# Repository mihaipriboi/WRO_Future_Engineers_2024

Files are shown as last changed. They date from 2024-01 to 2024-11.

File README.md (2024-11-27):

<center><h1> Nerdvana Cancer 2024 </center>

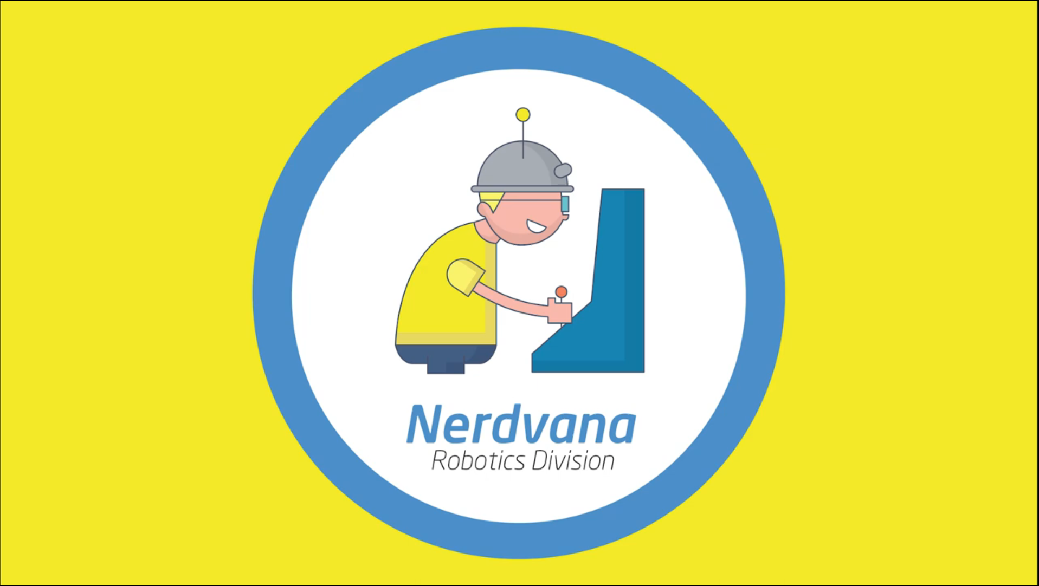
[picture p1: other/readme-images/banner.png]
Banner







This repository contains the documentation for the Nerdvana Cancer team's robot for the 2024 World Robot Olympiad Future Engineers competition. The robot, was designed and built by a team of three students.

## Table of Contents
* [The Team](#team)
* [The Challenge](#challenge)
* [The Robot](#robot-image)
* [Performance Video](#video)
* [Mobility Management](#mobility-management)
  * [Powertrain](#powertrain-mechanical)
    * [Drivetrain](#drivetrain-mechanical)
    * [Motor](#motor-mechanical)
    * [Motor Driver](#motor-driver-mechanical)
  * [Steering](#steering-mechanical)
    * [Servo Motor](#servo-motor)
  * [Chassis](#chassis-mechanical)
* [Power and Sense Management](#power-and-sense-management)
  * [Li-Po Battery](#li-po-battery)
  * [Arduino Nano ESP32](#arduino-nano-esp32)
  * [IMU](#imu-sensor)
  * [OpenMV Cam H7 R2](#openmv-cam-h7-r2)
  * [Voltage Regulator](#voltage-regulator)
  * [PCB Design](#pcb)
  * [Circuit Diagram](#circuit-diagram)
* [Code for each component](#code-for-each-component)
  * [Drive Motor](#drive-motor-code)
  * [Servo Motor](#servo-motor-code)
  * [Camera](#camera-code)
  * [IMU](#gyro-sensor-code)
* [Obstacle Management](#obstacle-management)
  * [Qualification Round](#quali-management)
  * [Final Round](#final-management)
  * [Additional code](#additional-code)
* [Robot Construction Guide](#robot-construction-guide)
  * [Step 0: Print the 3D parts](#3d-printing)
  * [Step 1: Assemble the steering system](#steering-system-assembly)
  * [Step 2: Assemble the powertrain](#powertrain-assembly)
  * [Step 3: Attach the electronics](#electronics-attachment)
  * [Step 4: Attach the wheels](#wheel-attachment)
  * [Step 5: Final touches](#final-touches)
  * [Step 6: Upload the code](#code-upload)
* [Cost Report](#cost-report)
  * [3D Printing Costs](#3d-printing-costs)
  * [Other Parts Tested](#other-parts-tested)
  * [Tools and Equipment](#tools-and-equipment)
  * [Summary of Costs](#summary-of-costs)
* [Randomizer](#randomizer)
* [Resources](#resources)
  * [3D Models](#3d-models-resources)
  * [Images](#images-resources)
* [License](#copyright)

---

## The Team 

### Nicola Victor Teodor
<p align="center">
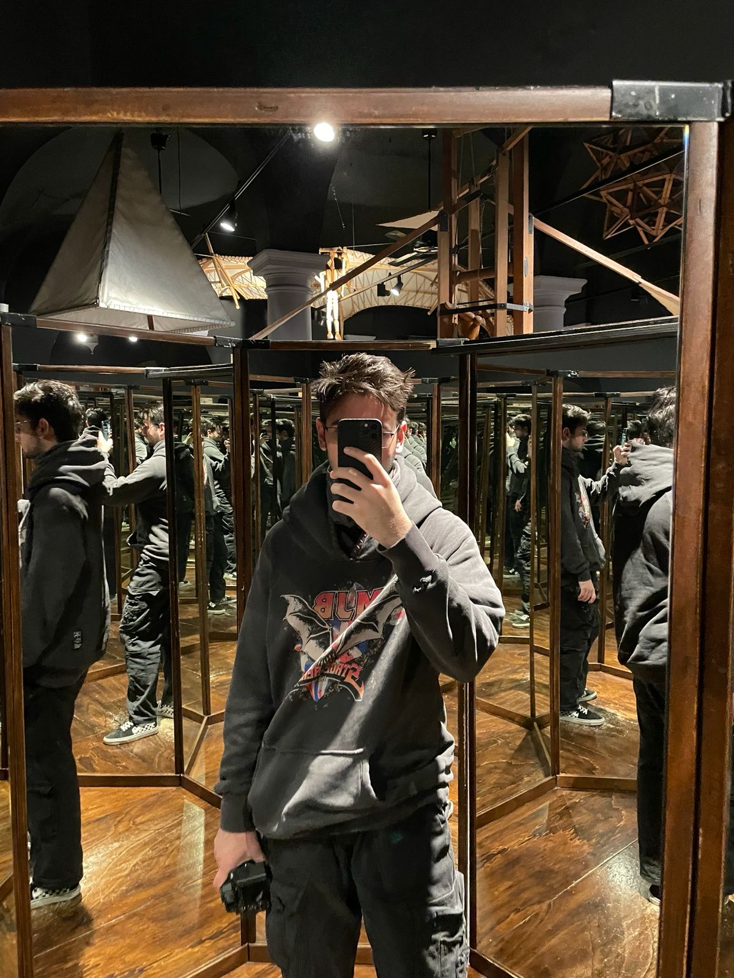
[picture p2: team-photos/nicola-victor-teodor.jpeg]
Nicola Victor Teodor
  
</p>

<b>Age:</b> 18

<b>High School:</b> National College of Informatics "Tudor Vianu", Bucharest

<b>Description:</b> Hi! I’m Victor from Romania and this is my second WRO season. Last year I participated in the RoboMission category and this year I wanted a new challenge. I own the fact that I’m a huge nerd: from coding and robotics, to photography, cinema, music, guitar, and even Formula 1.

---

### Bălan Teodor Ovidiu
<p align="center">
  Bălan Teodor Ovidiu
</p>

<b>Age:</b> 19

<b>University:</b> University of Bucharest

<b>Description:</b> Wassup y'all! My name is Teodor, and I love traveling and experiencing new things. Since I was a kid, I’ve always been drawn to solving puzzles, playing basketball, discovering new inventions, and thinking of creative ways to do things. Also, I know how to do a backflip. 🤠

---

### Priboi Luca Mihai
<p align="center">
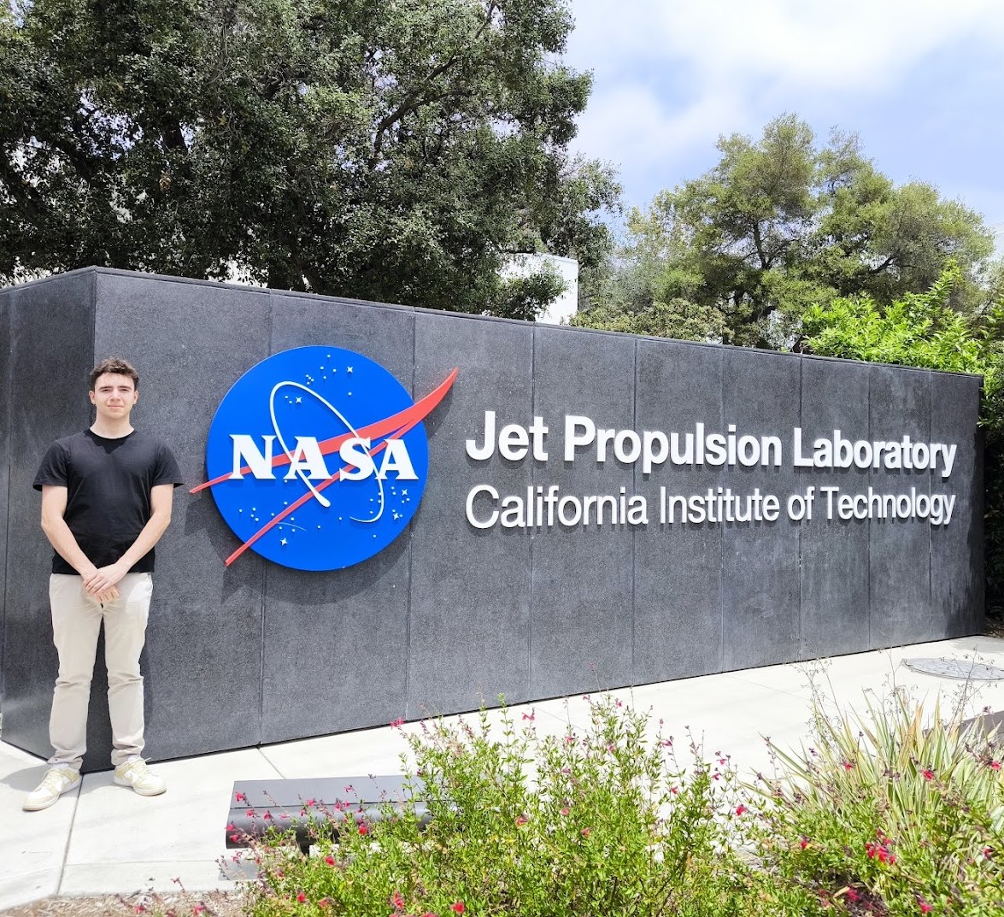
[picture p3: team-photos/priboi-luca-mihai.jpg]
Priboi Luca Mihai
  
</p>

<b>Age:</b> 19

<b>University:</b> Politehnica University of Bucharest

<b>Description:</b> Hello! I am Mihai! I've been participating at WRO since 2015 and I am very excited to be part of the Nerdvana Romania team. My academic passions are programming, physics and robotics, but I also enjoy playing the piano 🎹, whatching movies 🎬, traveling ✈️ and Formula 1 🏎️🏁.

---

### Tuțu Mihai Alexandru
<p align="center">
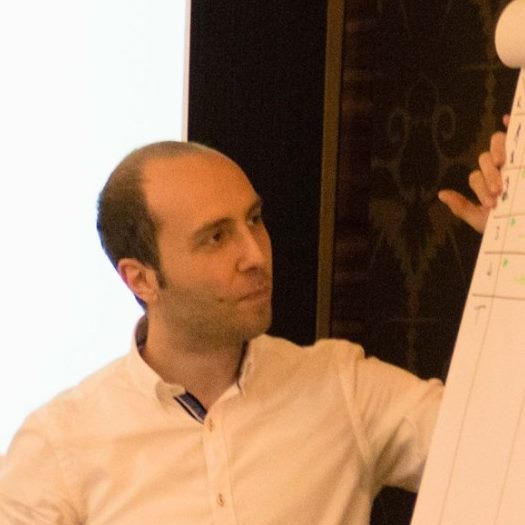
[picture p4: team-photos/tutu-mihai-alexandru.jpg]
Tuțu Mihai Alexandru
  
  <p align="center">Nerdvana Romania Founder</p>
</p>

<b>Role:</b> Coach

<b>Description:</b> Hard working young man, objective driven and ready for the long haul. I like challenges and I never back down. The harder, the better. I like being pushed over my limits just to prove myself I can do better.

Very social, I can easily blend in a team. Like to communicate a lot with others and to coordinate with other teammates. I was led and I led teams to certain objectives. I believe the only way to get where you want is to never stop trying and to never give up until you reach your destination.

---

### Priboi Maria Marcela
<p align="center">
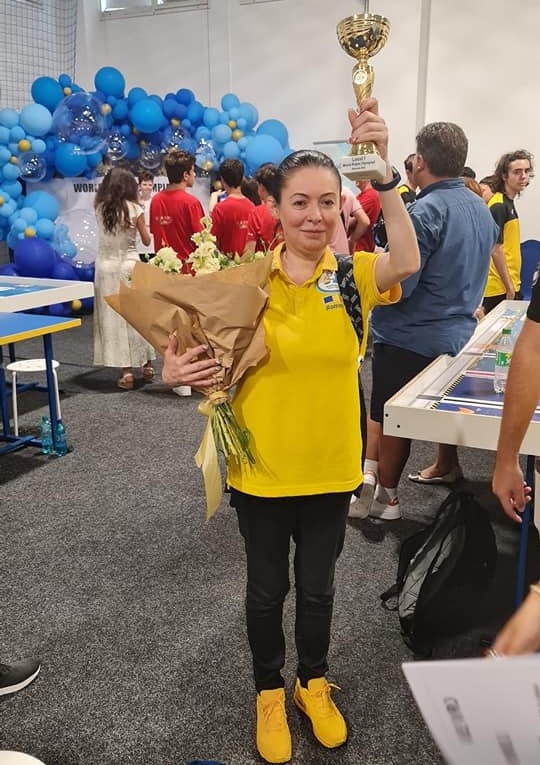
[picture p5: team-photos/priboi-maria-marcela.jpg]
Priboi Maria Marcela
  
  <p align="center">Nerdvana Romania Founder</p>
</p>

<b>Role:</b> Manager

<b>Description:</b> I am a very ambitious person, I like to work hard and to be involved in many projects. I am a very organized person and I like to have everything planned. I am a very sociable person and I like to communicate with people. I am a very responsible person and I like to take care of everything that is happening around me. I am a very creative person and I like to come up with new ideas. I am a very determined person and I like to achieve my goals.

---

### Team photo
<p align="center">
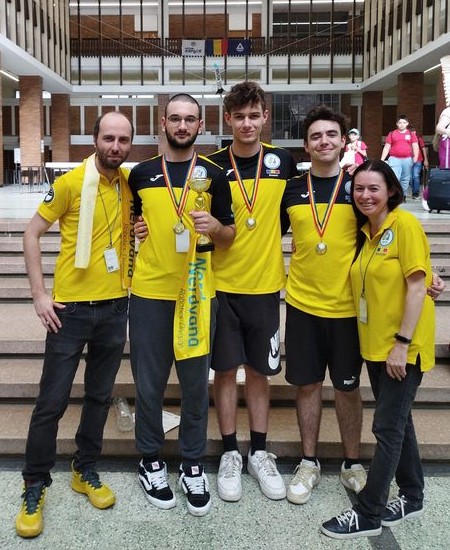
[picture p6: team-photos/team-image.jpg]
Team
  
</p>

## The Challenge 

The **[WRO 2024 Future Engineers - Self-Driving Cars](https://wro-association.org/)** challenge invites teams to design, build, and program a robotic vehicle capable of driving autonomously on a racetrack that changes dynamically for each round. The competition includes two main tasks: completing laps while navigating randomized obstacles and successfully performing a precise parallel parking maneuver. Teams must integrate advanced robotics concepts such as computer vision, sensor fusion, and kinematics, focusing on innovation and reliability.

This challenge emphasizes all aspects of the engineering process, including:
- **Mobility Management:** Developing efficient vehicle movement mechanisms.
- **Obstacle Handling:** Strategizing to detect and navigate traffic signs (red and green markers) within specified rules.
- **Documentation:** Showcasing engineering progress, design decisions, and open-source collaboration through a public GitHub repository.

Points are awarded based on performance in the challenge rounds, quality of the engineering documentation, and the ability to create an innovative and robust solution. The goal is to inspire STEM learning through real-world robotics applications, teamwork, and creative problem-solving.

Learn more about the challenge [here](https://wro-association.org/wp-content/uploads/WRO-2024-Future-Engineers-Self-Driving-Cars-General-Rules.pdf).

## Photos of our robot MOOYA (Mechanized Optimization for Outstanding Yield and Adaptation) 

|  |  | 
| :--: | :--: |
| *Front* | *Back* |
|  |  | 
| *Left* | *Right* |
|  |  | 
| *Top* | *Bottom* |

<br>

## Our video of the robot on [Youtube](https://www.youtube.com/watch?v=aLT0-nPUaAE) 

<br>

# Mobility Management 
<!-- ![Powertrain](./images/resources/powertrain.png "Powertrain") -->

The robot's mobility is managed by a combination of components, including the powertrain, steering system, and chassis. These elements work together to ensure the robot's smooth and efficient movement.

## Powertrain 

<!-- ![Powertrain - Bottom View](./images/resources/powertrain_bottom_text.png "Powertrain - Bottom View") -->

### Drivetrain 

To minimize friction and thereby reduce speed loss, driving axle was made from lego pieces. We conected the motor to the driving axle using a custom 3D-printed adapter. The driving axle has a rear wheel lego differential, which allows the robot to turn smoothly. As the axle was already lego, we used lego wheels.

<br>

**Potential Improvements**:
- Upgrade to a stronger or more precise differential for smoother turning.
- Test alternative materials for the Lego driving axle to reduce weight and increase durability.
- Replace the 3D-printed adapter with a metal one to improve robustness and reliability.

### Motor 

<table>
  <tr>
    <td width="50%" style="text-align: left;">
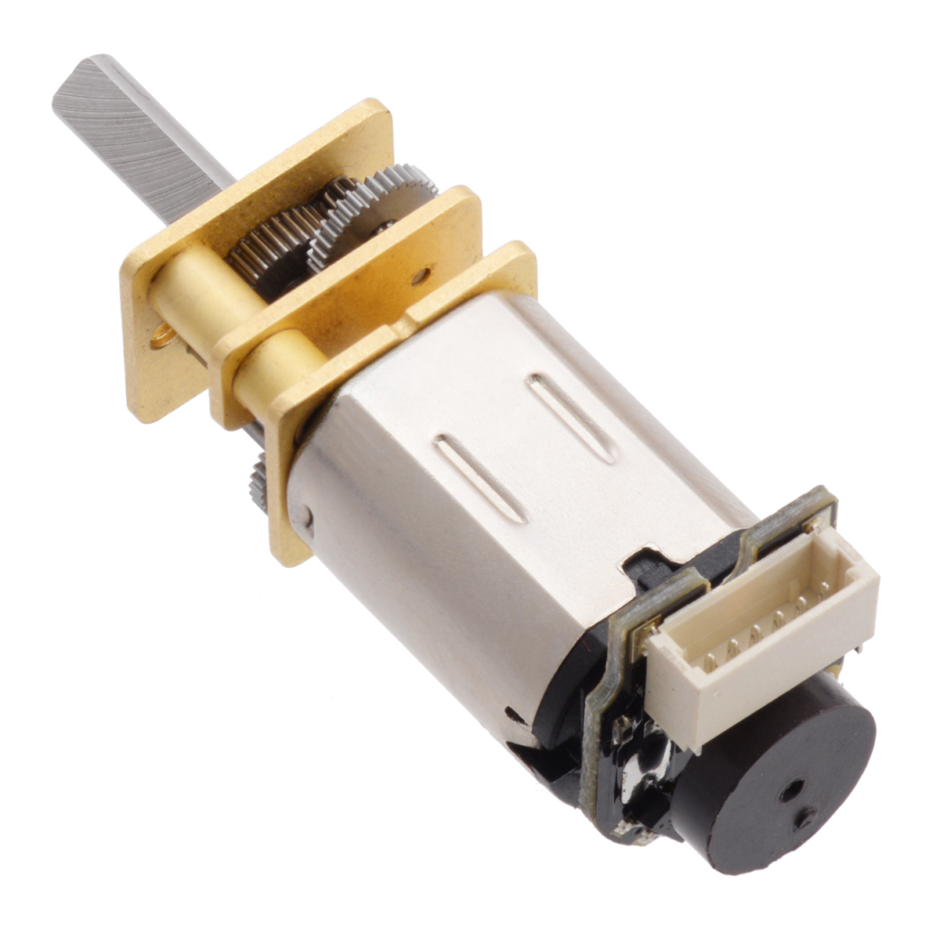
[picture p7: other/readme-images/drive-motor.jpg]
DC Gearmotor
      
    </td>
    <td width="50%" style="text-align: left; vertical-align: top;">
      <h3>Specifications:</h3>
      <li>Voltage: 12V</li>
      <li>Gear Ratio: 1:50</li>
      <li>Speed: 650 ± 31% rpm</li>
      <li>Torque: 0.67 ± kg·cm</li>
      <li>Weight: 9.5g</li>
      </li>
    </td>
  </tr>
</table>

Following an evaluation of different motors, we settled on a micro DC gear motor on which we attached a magnetic encoder. This motor was selected for its lightweight and compact design, which stands out among others with comparable output. Additionally, the magnetic encoder offers greater precision than its optical counterpart. We secured the motor to the chassis using a custom 3D-printed holder.

Where to buy the motor: https://www.pololu.com/product/3039

To connect the motor's axle to a Lego-compatible axle, we created a custom 3D-printed adapter.

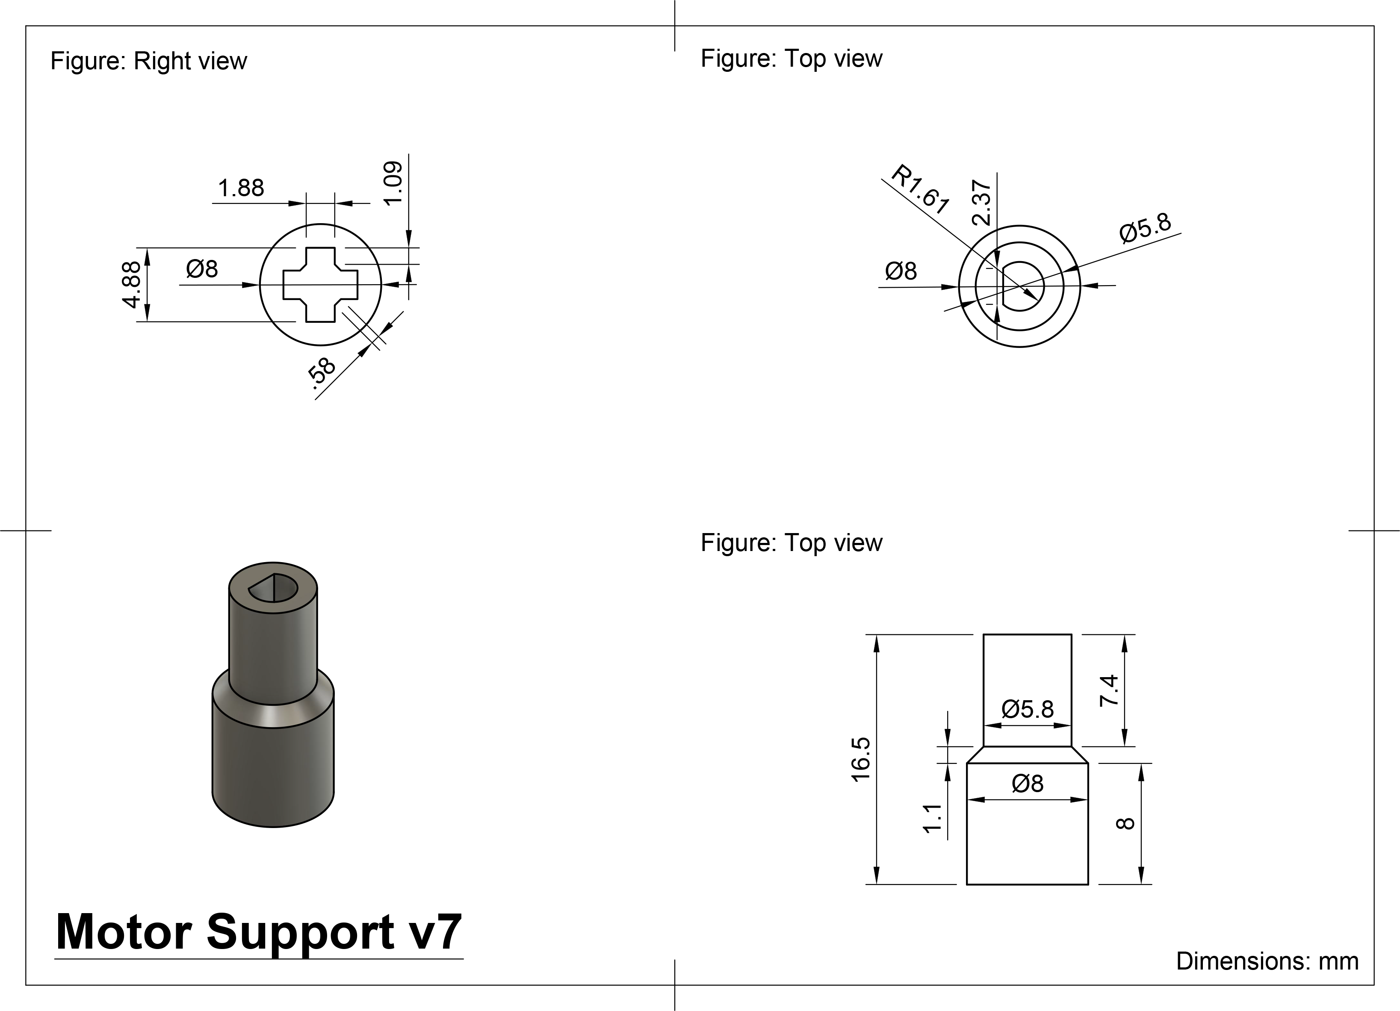
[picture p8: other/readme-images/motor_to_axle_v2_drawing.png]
Gearmotor to axle - 3D Model Gearmotor to axle 3D piece


To secure the motor to the chassis, we designed a custom 3D-printed holder. The holder is split into two halves, which are then screwed together to ensure the motor remains in place.

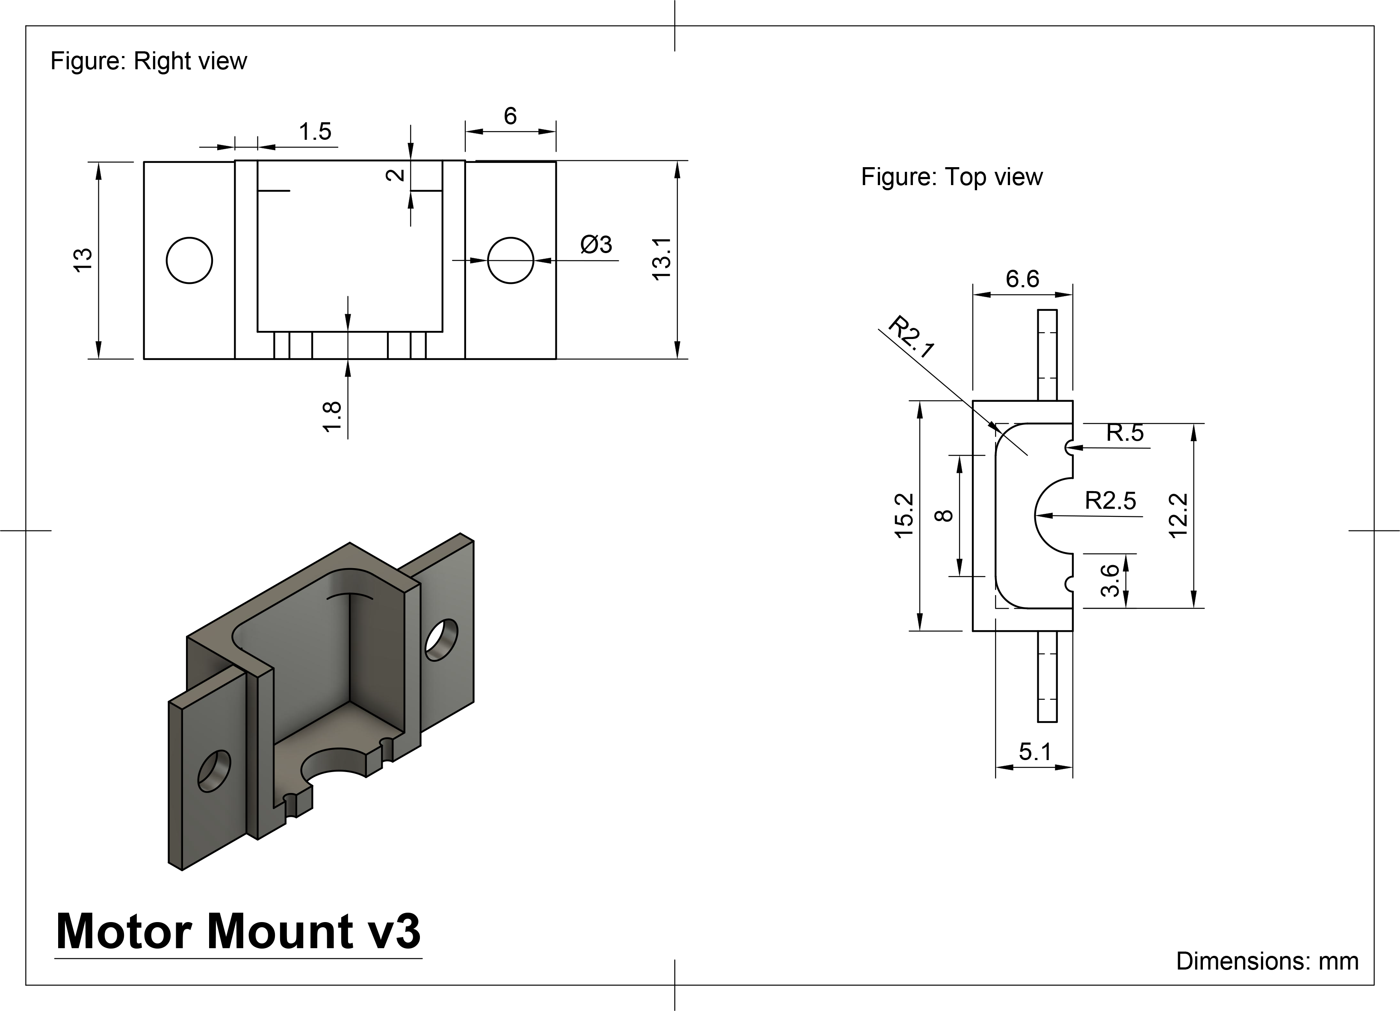
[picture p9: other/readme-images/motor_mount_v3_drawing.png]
Micro motor holder (half) - 3D Model Micro motor holder (half) 3D piece


<br>

**Potential Improvements**:
- Consider upgrading to a brushless motor for higher efficiency and better thermal management.
- Implement a more robust motor holder to prevent vibrations and ensure stability.
- Explore alternative motor designs to enhance performance and reduce weight.

### Motor Driver 

<table>
  <tr>
    <td width="50%" style="text-align: left;">
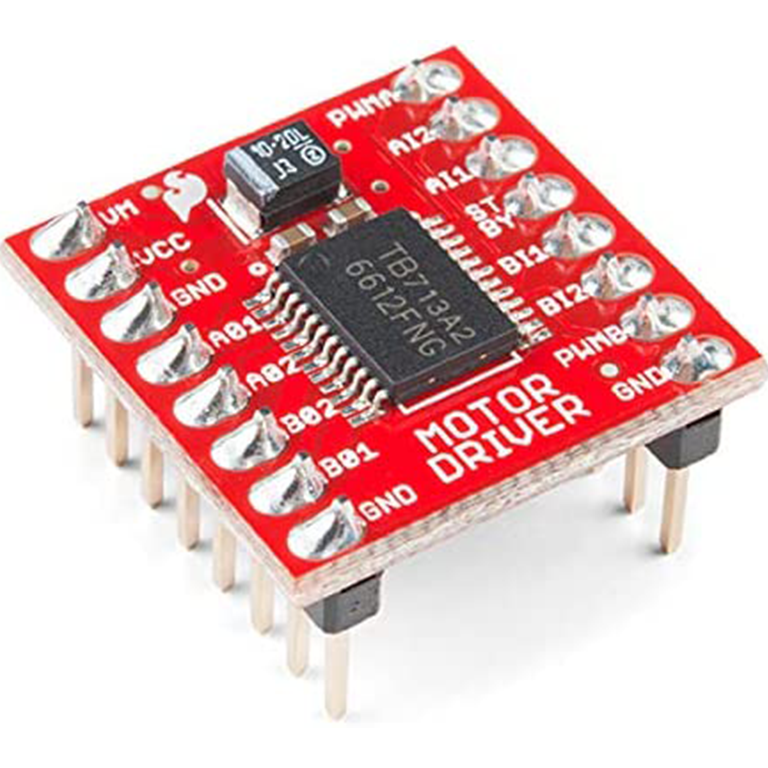
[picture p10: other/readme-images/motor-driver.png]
Motor driver
      
    </td>
    <td width="50%" style="text-align: left; vertical-align: top;">
      <h3>Specifications:</h3>
      <li>Power supply voltage: VM = 15V max, VCC = 2.7--5.5V</li>
      <li>Output current: Iout = 1.2A (average) / 3.2A (peak)</li>
      <li>Standby control to save power</li>
      <li>CW/CCW/short-brake/stop motor control modes</li>
      <li>Built-in thermal shutdown circuit and low-voltage detecting circuit</li>
    </td>
  </tr>
</table>

To control the speed of the drive motor, we utilized a SparkFun Dual TB6612FNG motor driver.

Where to buy the motor driver: https://www.sparkfun.com/products/14450

<br>

**Potential Improvements**:
- Replace the motor driver with a custom PCB to reduce weight and improve space utilization.
- Add active cooling or heat sinks for enhanced thermal performance during extended use.
- Explore higher-current motor drivers to accommodate potential motor upgrades.
- Implement a more robust power management system to ensure reliable operation.

## Steering 

<!-- ![Powertrain - Angled Bottom View](./images/resources/bottom_angle.png "Powertrain - Angled Bottom View") -->

After experimenting with various steering mechanisms such as Ackermann steering and bell-crank steering, we assessed their advantages and drawbacks. Ultimately, we chose a straightforward steering system consisting of a parallelogram linkage. This decision was made because the alternative systems were either too large or too complex to implement effectively. Our selected mechanism is simple, light, and compact, providing a satisfactory steering angle. While it does not adhere to the Ackermann steering geometry, our tests showed that for our robot's small size and light weight, this omission was not critically significant.

As an upgrade to last year's design, we replaced the Lego-based steering system with a custom 3D-printed one. This change allowed us to reduce the robot's weight and size, while also enhancing its overall performance. The new steering system is more robust and offers greater flexibility in terms of design and implementation.

The steering system is composed of 2 symmetrical wheel holders, that are conected togheter by a steering arm. The steering arm is conected to the servo motor. The joints between the wheel holders and the steering arm are made using steel rods.

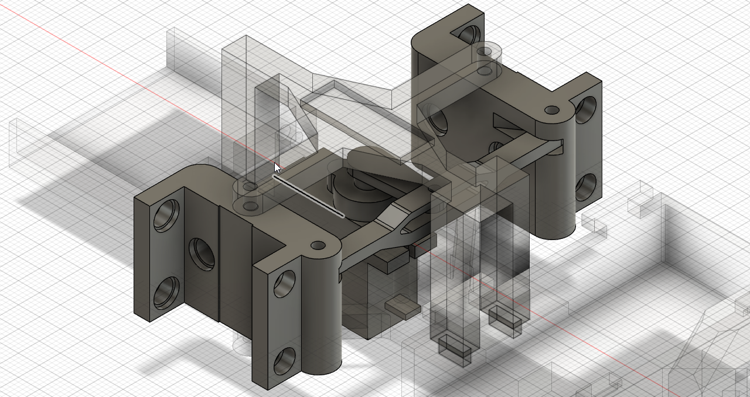
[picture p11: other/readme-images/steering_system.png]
Steering System


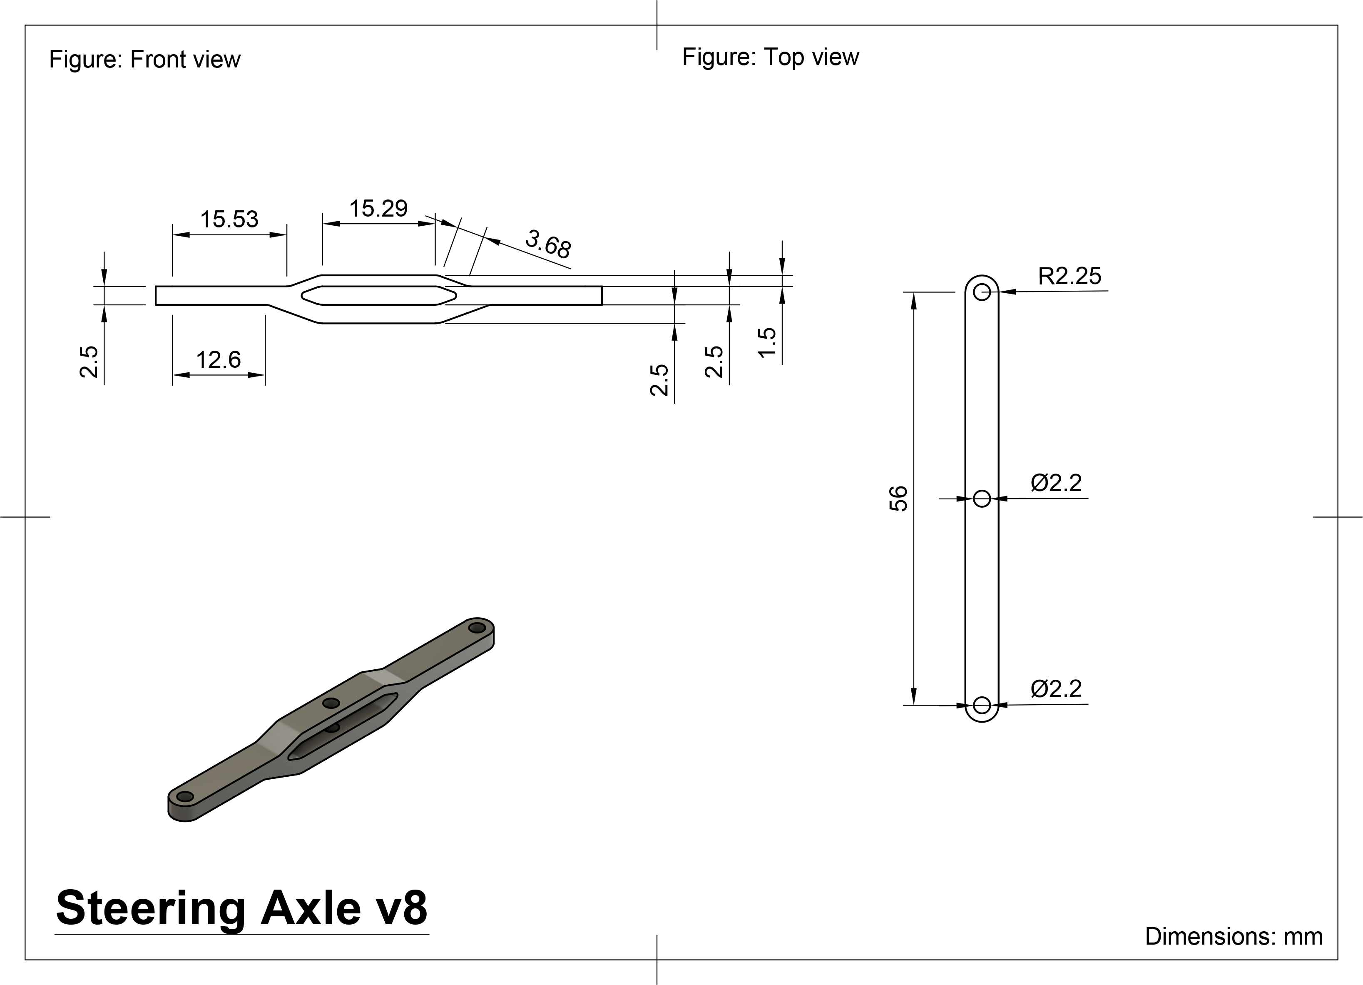
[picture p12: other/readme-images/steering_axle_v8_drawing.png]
Steering Axle


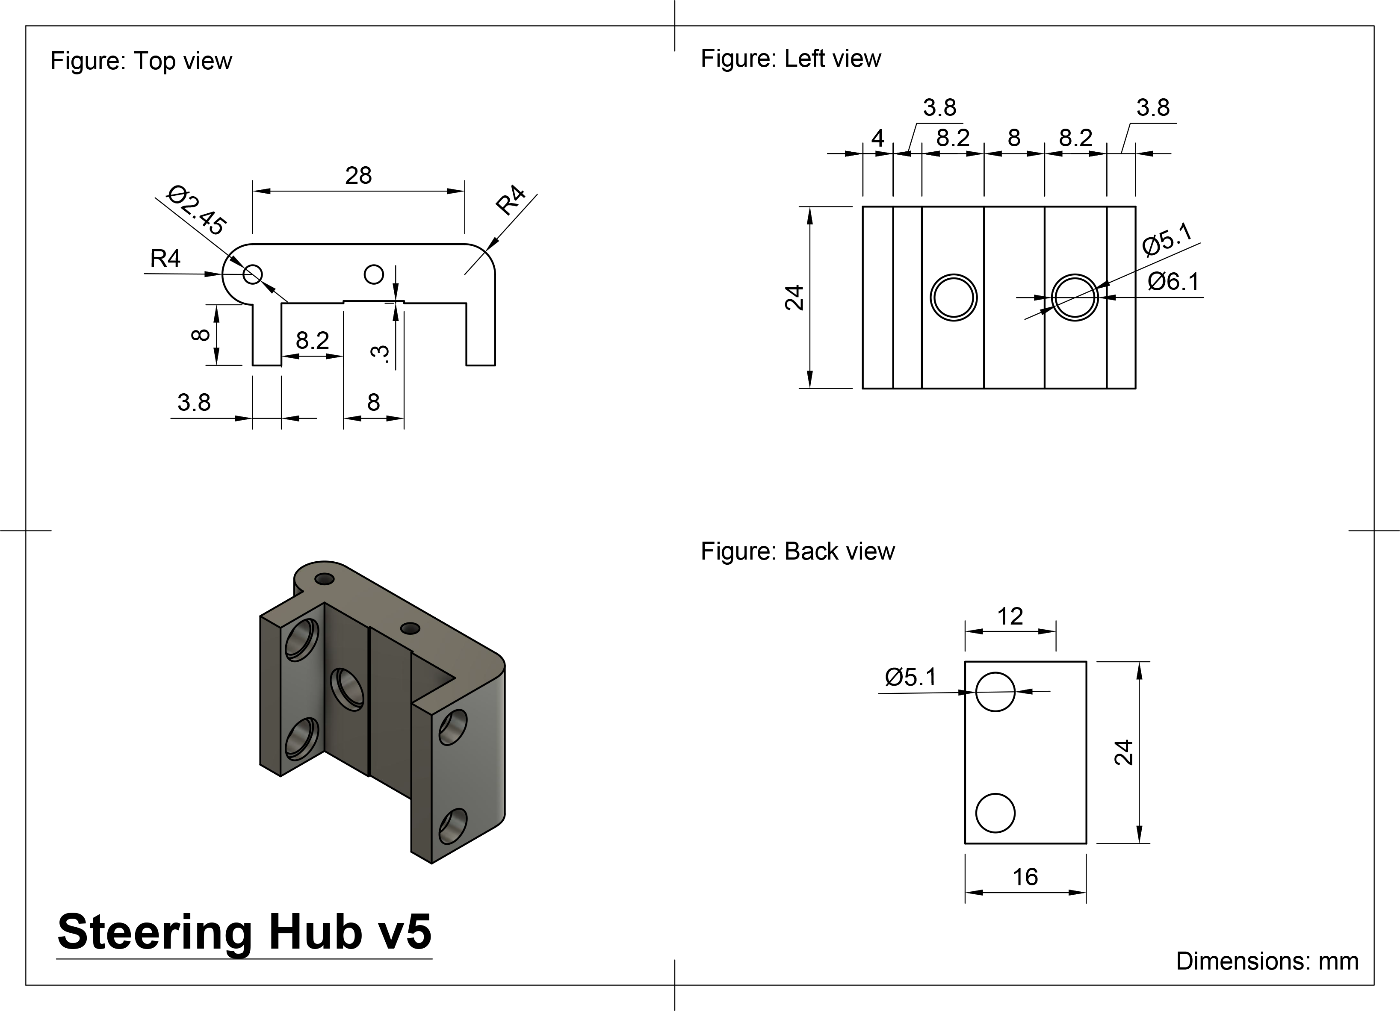
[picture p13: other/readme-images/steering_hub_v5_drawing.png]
Steering Hub


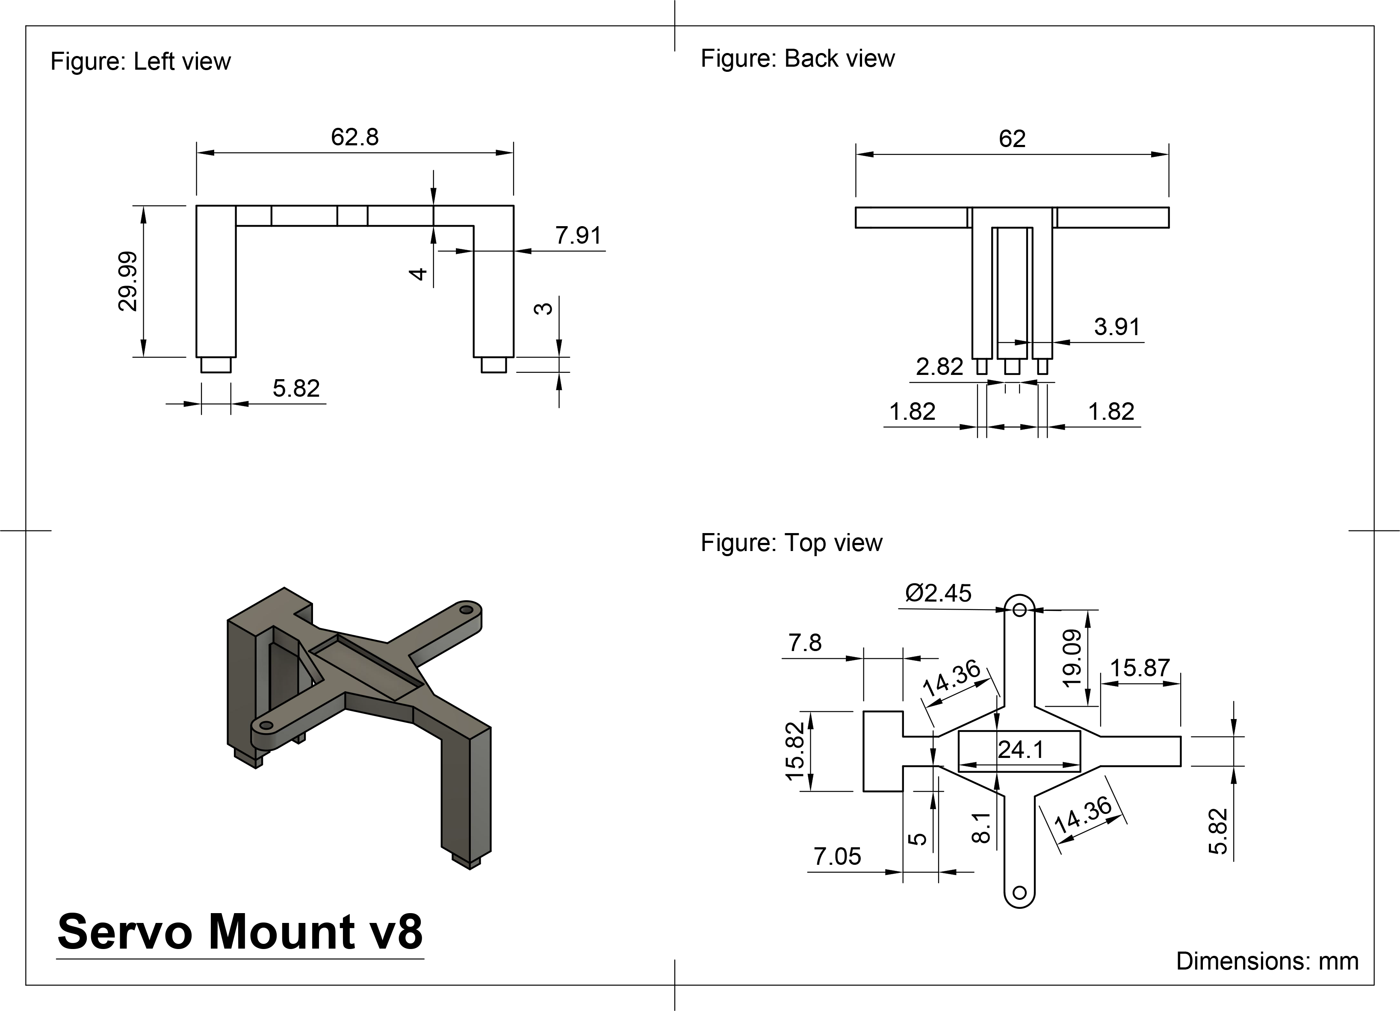
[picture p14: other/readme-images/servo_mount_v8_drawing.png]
Servo Mount


<br>

**Potential Improvements**:
- Make the steering angle wider to improve the robot's turning radius.
- Implement Ackermann steering geometry for more precise and efficient turning.
- Use ball-bearing joints in the linkage to reduce friction and increase durability.
- Replace the 3D-printed components with lightweight aluminum for greater strength.

### Servo Motor 

<table>
  <tr>
    <td width="50%" style="text-align: left;">
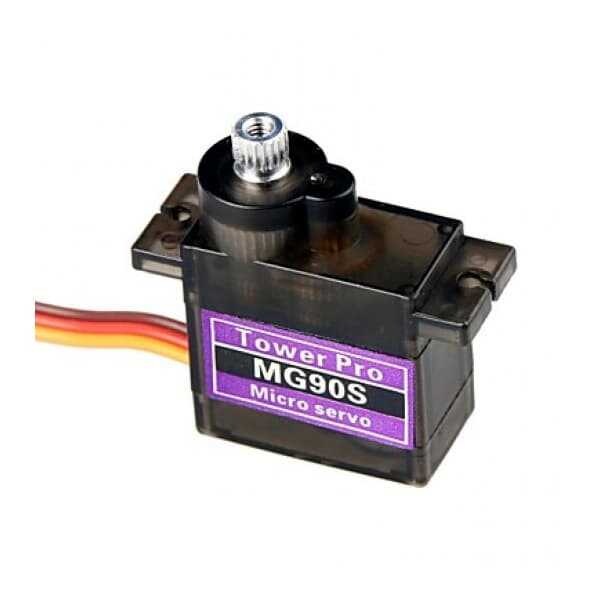
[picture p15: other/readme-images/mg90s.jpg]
Servo Motor
      
    </td>
    <td width="50%" style="text-align: left; vertical-align: top;">
      <h3>Specifications:</h3>
      <li>Weight: 13.4g</li>
      <li>Stall torque: 2.2 kgf·cm (6V)</li>
      <li>Operating speed: 0.08 s/60 degree (6V)</li>
      <li>Rotation angle: 120 degree</li>
    </td>
  </tr>
</table>

For steering, we selected the MG90S servo motor, favoring it for its high torque and swift response.

Where to buy the servo motor: https://cleste.ro/motor-servo-mg90s-180g.html

<br>

**Potential Improvements**:
- Test servos with a wider rotation angle to improve steering flexibility.
- Integrate position feedback into the servo for real-time adjustment and enhanced precision.

## Chassis 

Our previous attempts at designing a robot for the Future Engineers category were bulky and heavy, mostly lego based. This year, we aimed to create a more compact and lightweight robot. We achieved this by using a almost entirely 3D-printed chassis. Because of this, the fact that we tried to use as few components as possible, the robot is aproximately 50% lighter than last year's robot, while also being more compact.

Another improvement we made was the way of connecting 3D parts togheter. Instead of using lego or screws, we used snapping joints and pins.

The chassis holds basically all of the components. Only the gearmotor and the gyroscope are attached to a separate piece that is then attached to the chassis. The back holds the differential; the middle part has a hole for the battery, on top of which the pcb is mounted using a 3d printed holder. The front holds the camera and the servo motor; the servo mount piece is attached to the chassis as well.

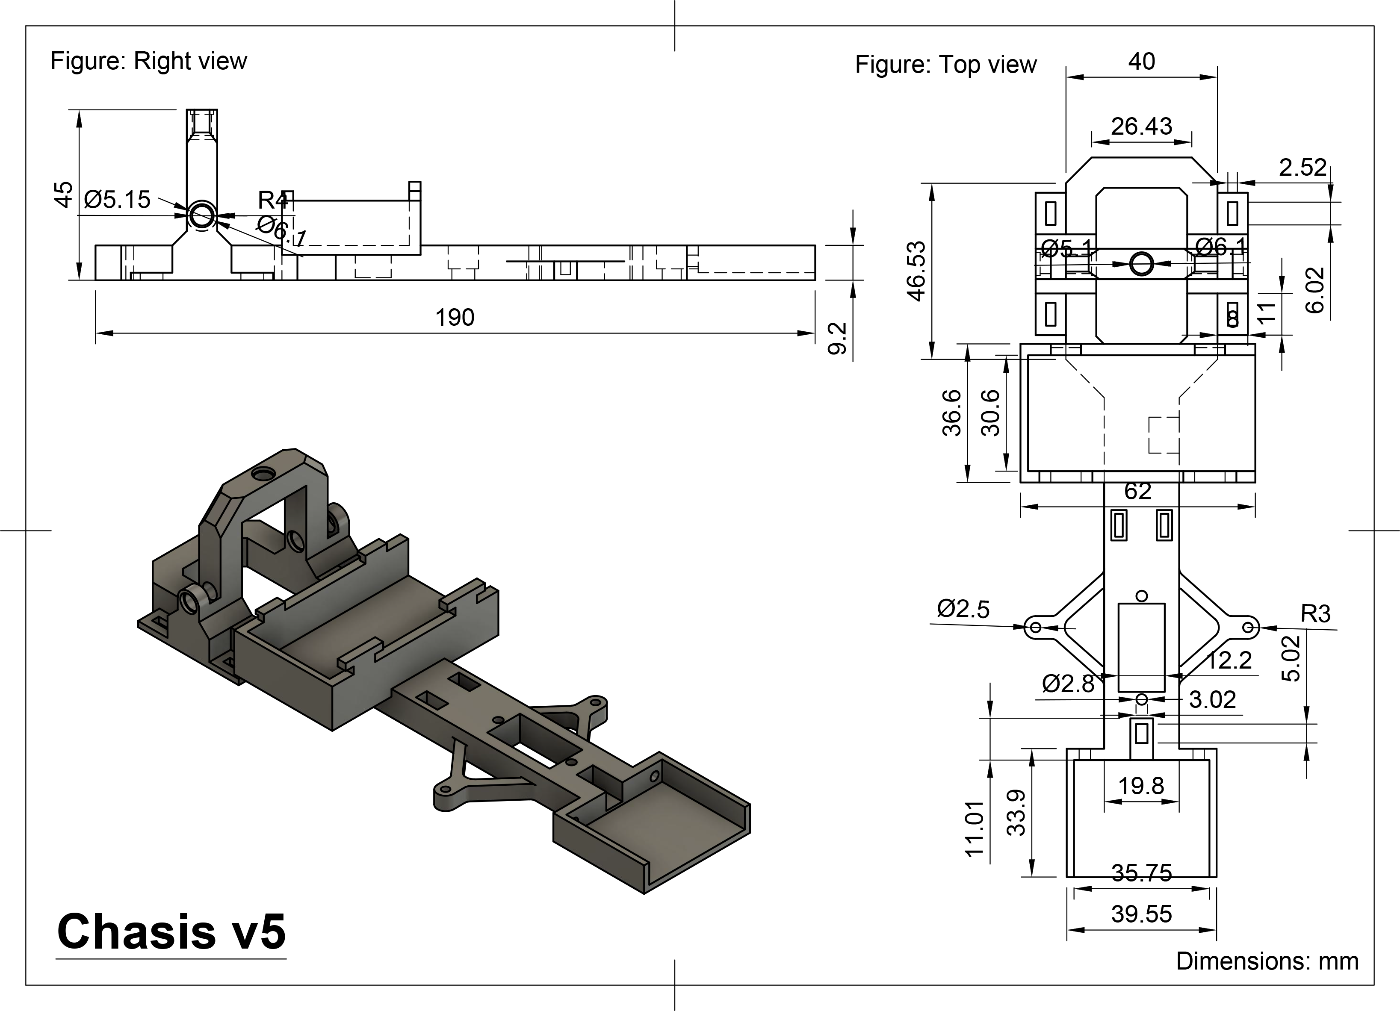
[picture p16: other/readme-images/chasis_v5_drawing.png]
Chassis


The motor support is a separate piece that holds the motor and the gyroscope. It is attached to the chassis using snapping joints.

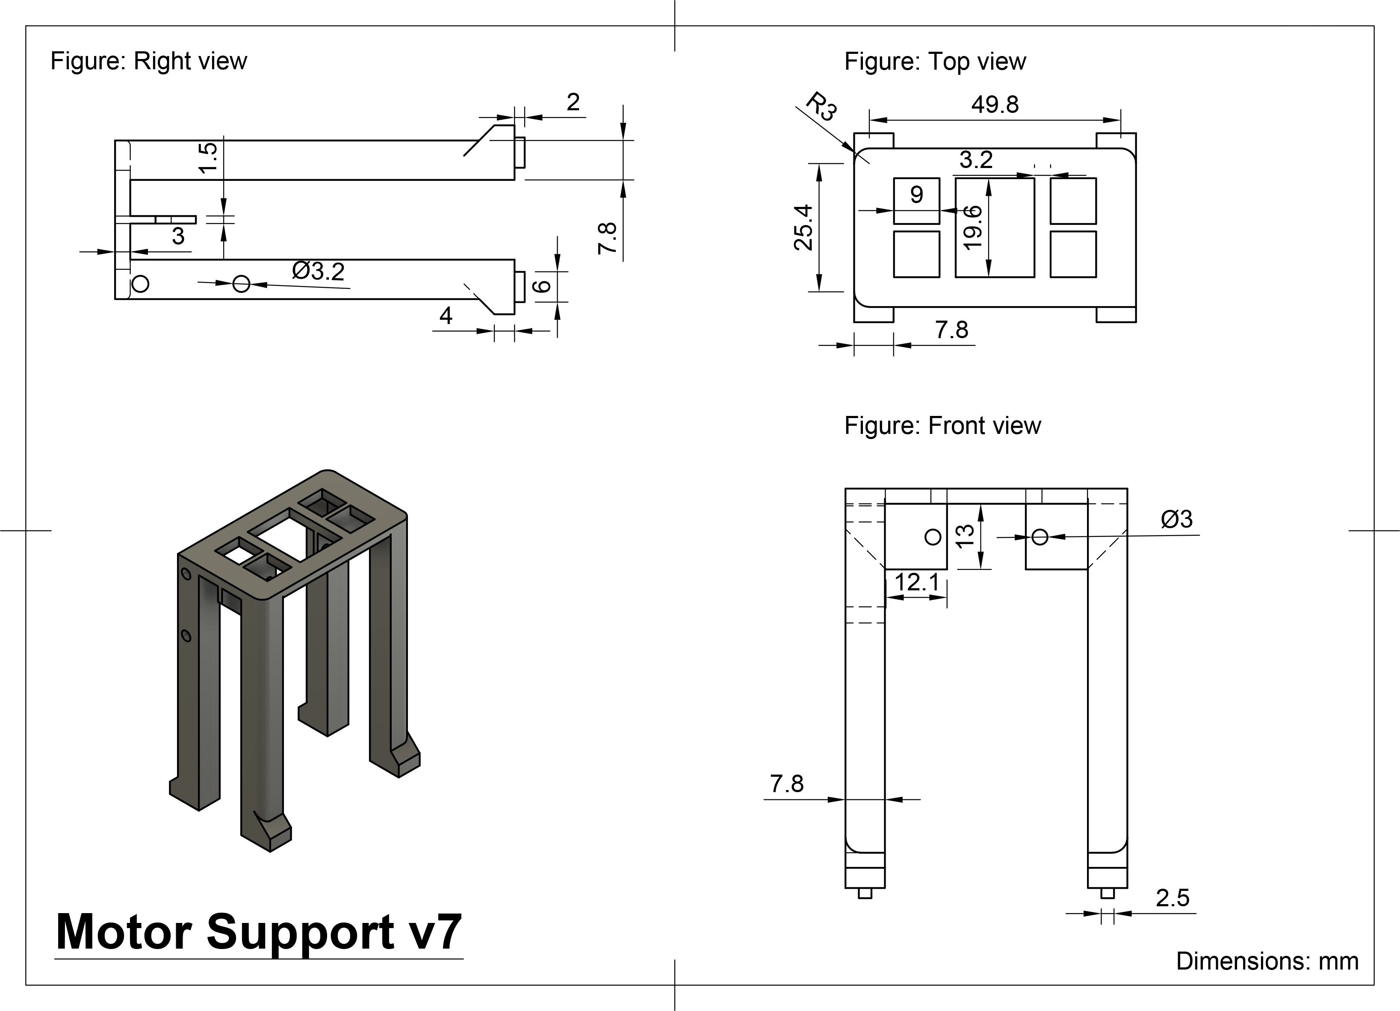
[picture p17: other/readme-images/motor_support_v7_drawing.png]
Motor Support


<br>

**Potential Improvements**:
- Add vibration-damping materials to minimize disturbances during operation.
- Test modular chassis designs for quicker assembly and maintenance.
- Implement a more aerodynamic shape to reduce drag and improve speed.
- Integrate a suspension system to enhance stability and shock absorption.
- Explore alternative materials for the chassis to improve durability and performance.
- Add a protective cover to shield the components from dust and debris.

# Power and Sense Management 

The robot's power and sense management system is composed of several components, including a Li-Po battery, an Arduino Nano ESP32, an IMU sensor, and an OpenMV Cam H7 R2. These components work together to provide the robot with the necessary power and sensory input to navigate its environment effectively.

### Li-Po Battery 

<table>
  <tr>
    <td width="50%" style="text-align: left;">
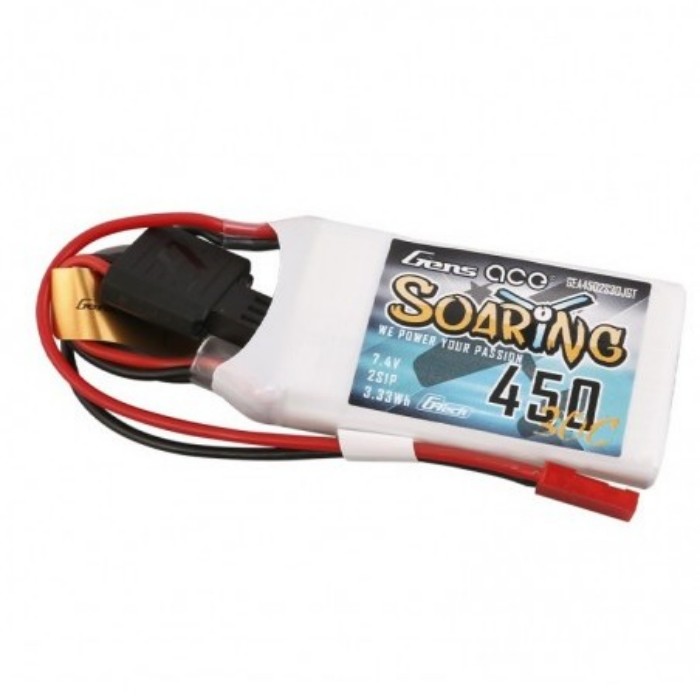
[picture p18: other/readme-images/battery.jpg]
Li-Po Battery
      
    </td>
    <td width="50%" style="text-align: left; vertical-align: top;">
      <h3>Specifications:</h3>
      <li>Capacity: 450mAh</li>
      <li>Voltage: 7.4V/2S</li>
      <li>Discharge rate: 30C</li>
      <li>Weight: 33 g</li>
      <li>Size: 56.5*31*9mm</li>
    </td>
  </tr>
</table>

Where to buy the battery: https://hpi-racing.ro/li-po-2s-74v/acumulator-lipo-gens-ace-g-tech-soaring-450mah-74v-30c-2s1p-cu-jst-syp.html

The battery is mounted using a custom 3D-printed holder, which is secured to the chassis.

<br>

**Potential Improvements**:
- Consider using a higher-capacity battery to extend runtime without increasing weight significantly.
- Add a battery management system (BMS) for better charging and discharging safety.
- Use quick-release connectors for easier battery replacement during competition.
- Implement a battery level indicator to monitor power consumption and remaining charge.

<!-- ![Battery Mount - 3D Model](./images/resources/BatteryMount.jpg "Battery Mount - 3D Model") -->

### Arduino Nano ESP32 

<table>
  <tr>
    <td width="50%" style="text-align: left;">
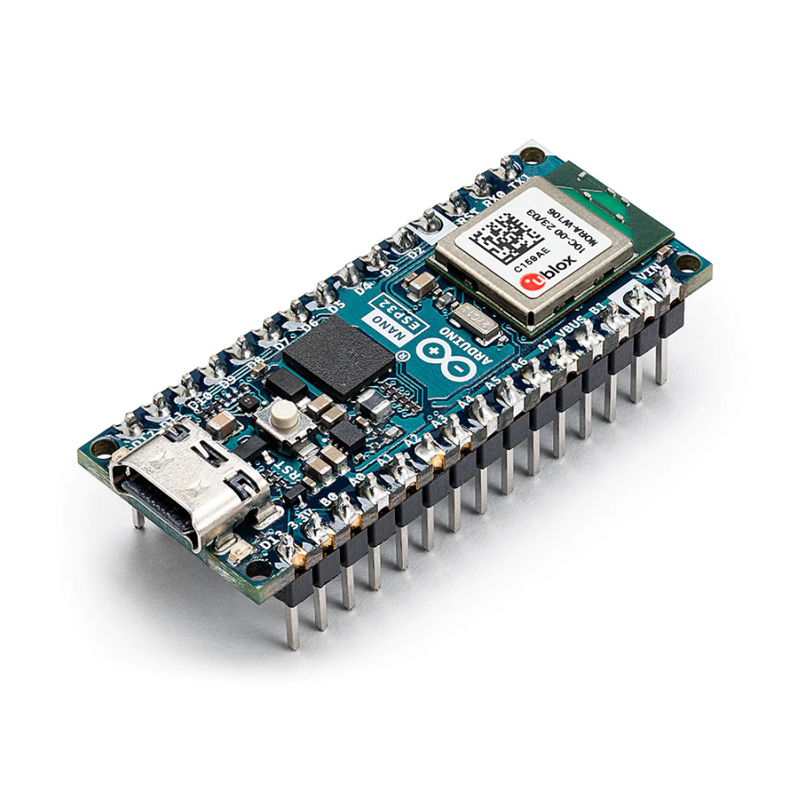
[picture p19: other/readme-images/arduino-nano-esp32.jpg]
Arduino Nano ESP32
      
    </td>
    <td width="50%" style="text-align: left; vertical-align: top;">
      <h3>Specifications:</h3>
      <li>Microcontroller: ESP32</li>
      <li>Flash memory: 4MB</li>
      <li>SRAM: 520KB</li>
      <li>Frequency: 240MHz</li>
      <li>Pins: 22</li>
      <li>Input voltage: 5V</li>
    </td>
  </tr>
</table>

At previous competitions, we used many microcontrollers to manage the robot's various components. This year, we opted for the Arduino Nano ESP32, which combines the functionalities of an Arduino Nano and an ESP32. This microcontroller is capable of handling all of the robot's sensors and actuators, providing a more streamlined and efficient solution.

Where to buy the Arduino Nano ESP32: https://store.arduino.cc/products/nano-esp32

The Arduino, mounted on a prototype board, is secured to the chassis with a 3D-printed holder. The pcb is attached to the chassis using screws.

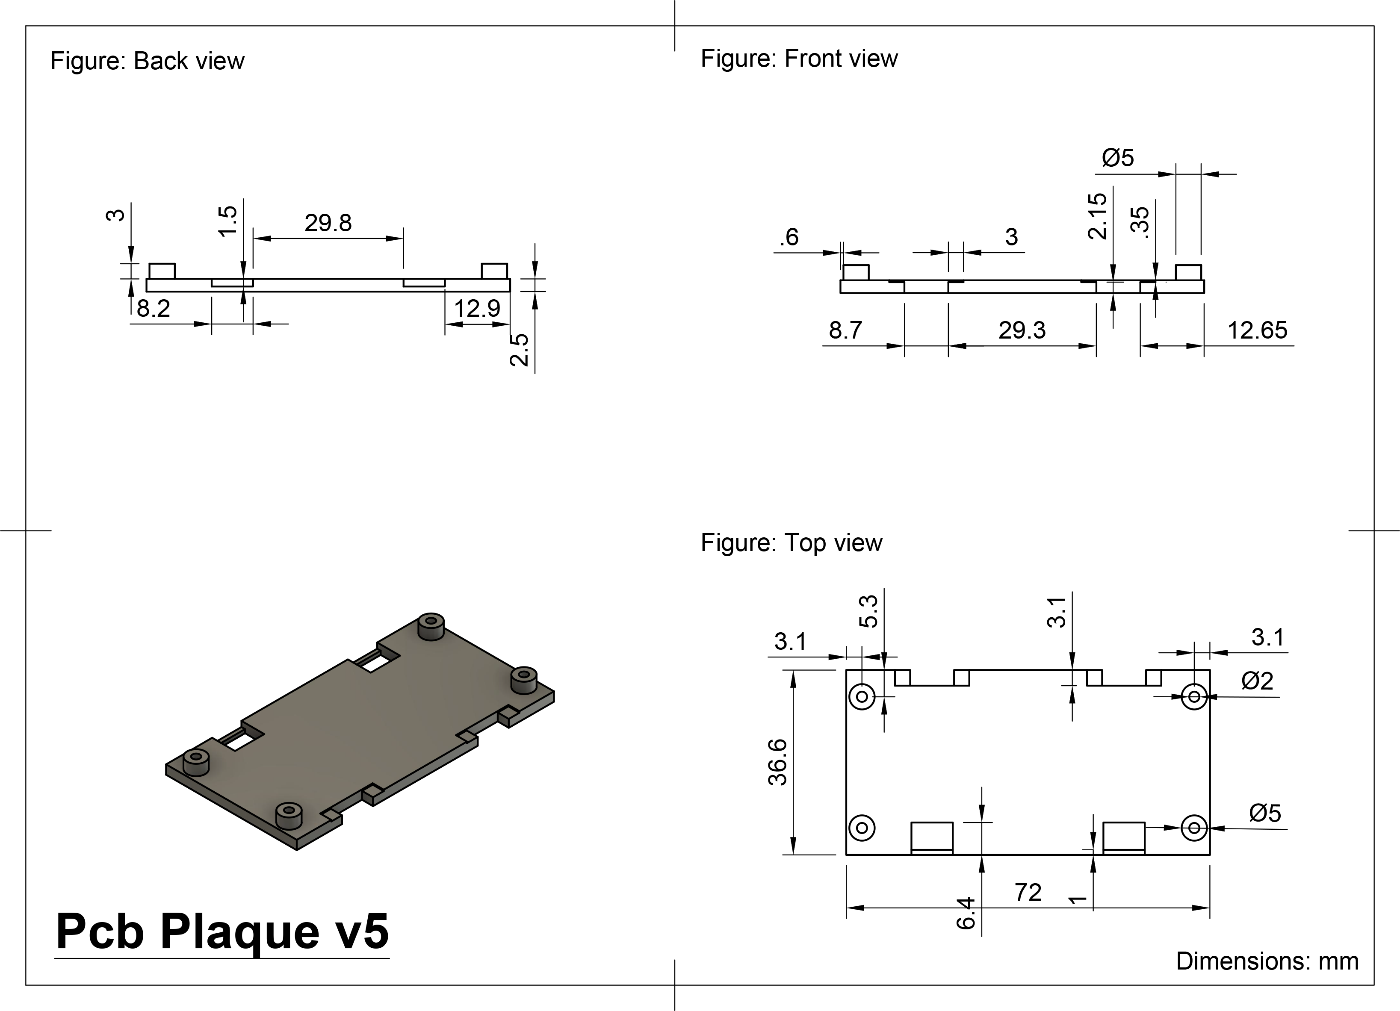
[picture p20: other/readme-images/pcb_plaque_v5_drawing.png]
PCB Mount


<br>

**Potential Improvements**:
- Design a custom PCB to integrate the Arduino Nano ESP32 with other components for a cleaner setup.
- Test alternative microcontrollers with additional processing power or I/O pins for future scalability.
- Optimize the mounting mechanism to allow easier access for debugging and repairs.
- Implement a power management system to ensure stable voltage supply and prevent damage to the microcontroller.

### IMU 

<table>
  <tr>
    <td width="50%" style="text-align: left;">
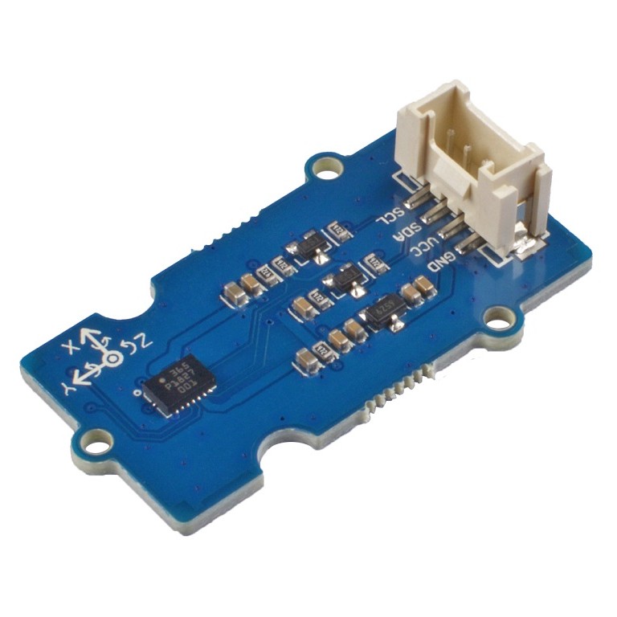
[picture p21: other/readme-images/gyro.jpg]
IMU Sensor - BMI088
      
    </td>
    <td width="50%" style="text-align: left; vertical-align: top;">
      <h3>Specifications:</h3>
      <li>Gyroscope range: ±2000°/s</li>
      <li>Accelerometer range: ±24g</li>
      <li>Interface: I2C</li>
      <li>Supply voltage: 1.71V to 3.6V</li>
      <li>Current consumption: 0.9mA</li>
    </td>
  </tr>
</table>

One importat aspect that helps the robot navigate is the inertial measurement unit (IMU). This sensor is based on BOSCH BMI088, which is a high-performance IMU with high vibration suppression. While the IMU measure the angular velocity and the acceleration of the robot, we only use the angular velocity to calculate the angle of the robot. The IMU is wired to the SDA and SCL pins on the arduino.

Where to buy the gyro sensor: https://www.seeedstudio.com/Grove-6-Axis-Accelerometer-Gyroscope-BMI088.html

<br>

**Potential Improvements**:
- Explore alternative IMU sensors with higher accuracy and better vibration resistance.
- Implement sensor fusion with additional sensors (e.g., magnetometer) for enhanced navigation.
- Test calibration procedures to minimize drift over longer runs.

### OpenMV Cam H7 R2 

<table>
  <tr>
    <td width="50%" style="text-align: left;">
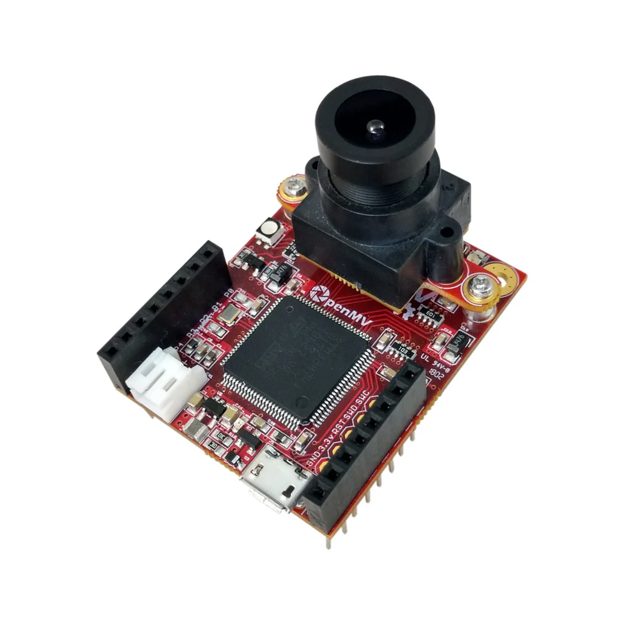
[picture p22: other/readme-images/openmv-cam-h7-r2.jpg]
OpenMV Cam H7 R2
      
    </td>
    <td width="50%" style="text-align: left; vertical-align: top;">
      <h3>Specifications:</h3>
      <li>Microcontroller: STM32H7</li>
      <li>Flash memory: 32MB</li>
      <li>RAM: 512KB</li>
      <li>Frequency: 480MHz</li>
      <li>Resolution: 640x480</li>
      <li>Frame rate: 60fps</li>
    </td>
  </tr>
</table>

The OpenMV Cam H7 R2 is a high-performance camera capable of color tracking. The best feature of this camera compared to other options (like the Pixy cam) is that is has a built-in microcontroller that can process the images and send the results to the Arduino. This way, the Arduino can focus on the robot's movement and the camera can focus on the image processing.

Together with the Arduino Nano ESP32, the camera delivers readings at approximately 60 frames per second.

Where to buy the OpenMV Cam H7 R2: https://openmv.io/products/openmv-cam-h7-r2

<br>

**Potential Improvements**:
- Upgrade to a camera with higher resolution for better object detection and tracking.
- Test alternative lighting solutions to improve visibility in various conditions.
- Implement advanced image processing algorithms to enhance detection accuracy.
- Use color correction algorithms: Apply color correction algorithms to compensate for any variations in lighting conditions. These algorithms can adjust the color values of the captured image to match a reference color space, making the colors more consistent and easier to calibrate.
- Provide user-adjustable parameters: Allow users to manually adjust color thresholds or ranges to fine-tune the color detection. This can be done through a user interface or by providing configuration files that can be modified.
- Implement real-time feedback: Display the detected colors in real-time to the user, along with the calibrated values. This allows users to visually verify the accuracy of the color detection and make adjustments if necessary.

### Voltage regulator 

<table>
  <tr>
    <td width="50%" style="text-align: left;">
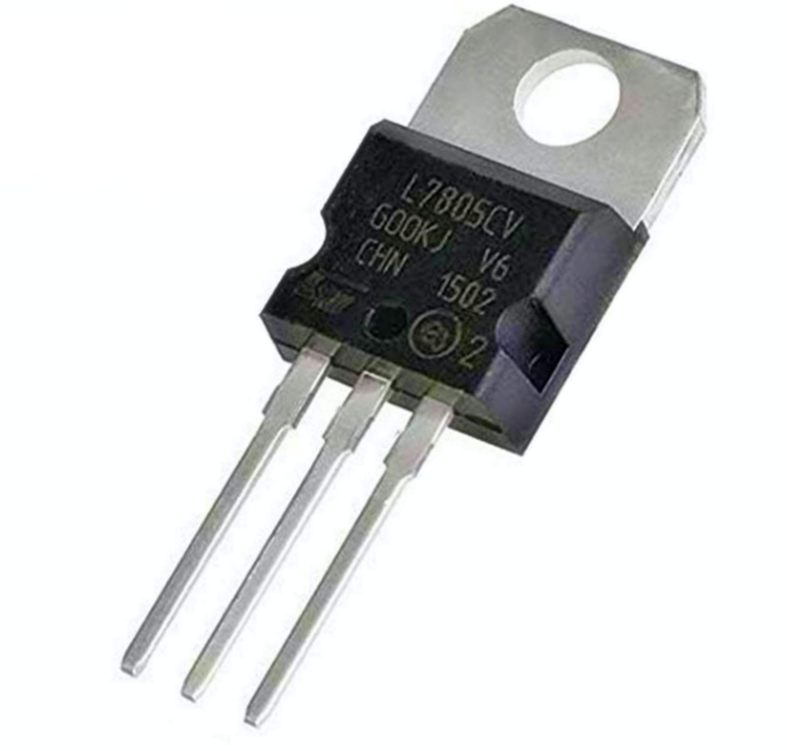
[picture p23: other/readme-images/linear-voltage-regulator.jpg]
Voltage regulator
      
    </td>
    <td width="50%" style="text-align: left; vertical-align: top;">
      <h3>Specifications:</h3>
      <li>Input voltage: 35V max</li>
      <li>Output voltage: 5V</li>
      <li>Output current: 1.5A</li>
      <li>Thermal shutdown circuit</li>
      <li>Short-circuit protection</li>
    </td>
  </tr>
</table>

To provide the Arduino Nano ESP32 with the required 5V, we needed to decrease the output from the 7.4V battery, which can reach up to 8.4V when fully charged. We employed a linear voltage regulator, the L7805CV, capable of converting input voltages below 35V down to a steady 5V.

Where to buy the 5V voltage regulator: https://ro.mouser.com/ProductDetail/STMicroelectronics/L7805CV?qs=9NrABl3fj%2FqplZAHiYUxWg%3D%3D

<br>

**Potential Improvements**:
- Replace the linear voltage regulator with a switching regulator for better efficiency.
- Add heat sinks to the regulator for improved thermal management.
- Design a compact custom regulator circuit to save space.

### PCB design 

The PCB was made on a prototype board. The board has a voltage regulator, the Arduino Nano ESP32, the motor driver, and connectors for the motor, the servo motor, the IMU, and the camera. The board is powered by the LiPo battery.

| PCB connections | PCB w/ regulator | PCB complete |
| :--: | :--: | :--: |
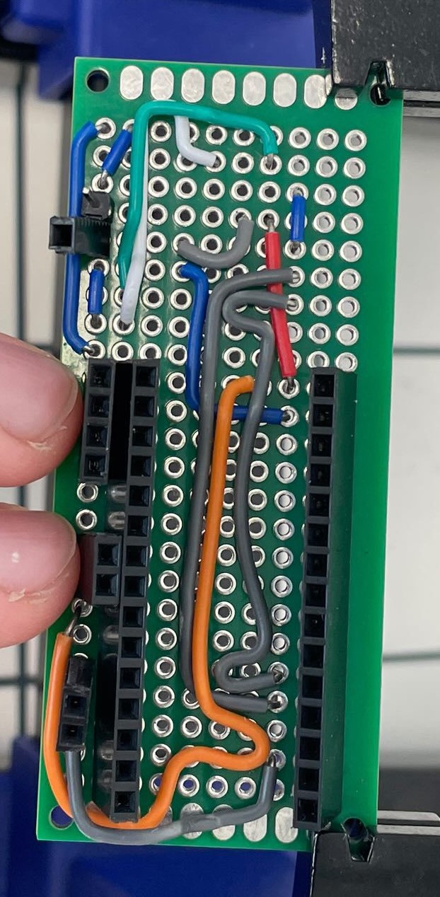
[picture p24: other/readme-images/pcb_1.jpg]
PCB connections
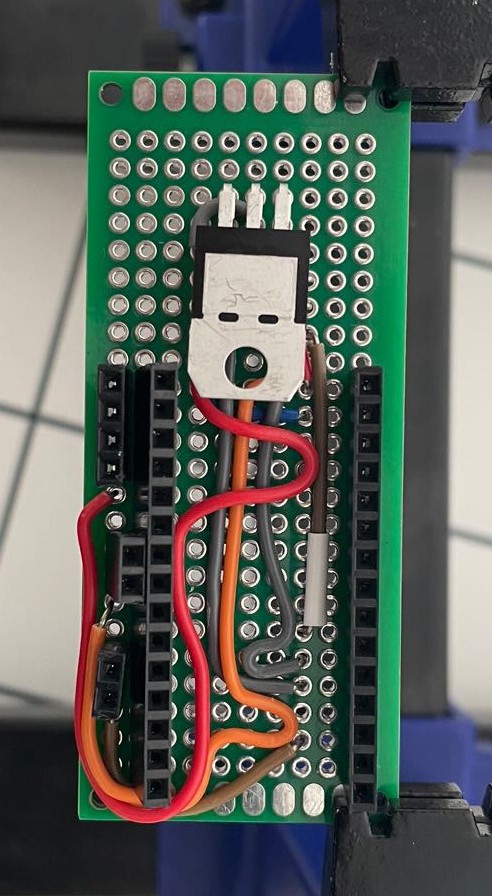
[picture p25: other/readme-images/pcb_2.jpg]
PCB w/ regulator
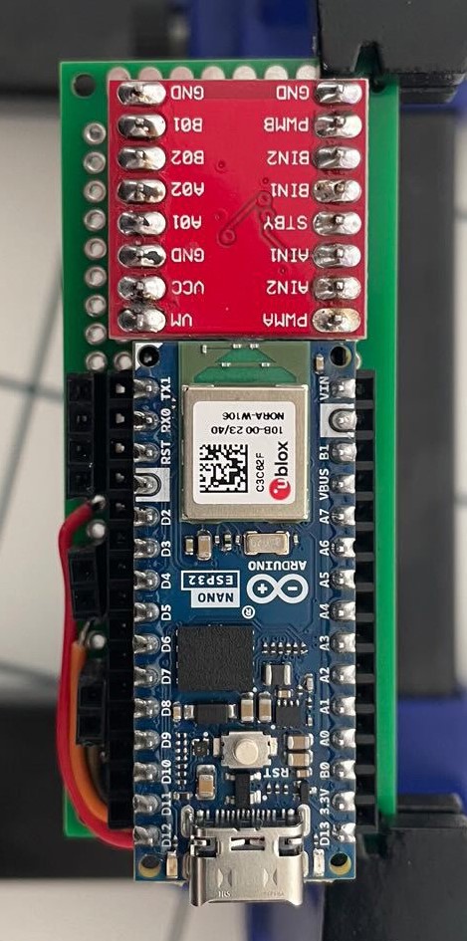
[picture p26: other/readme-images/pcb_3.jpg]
PCB complete
|  |  |  |

<br>

**Potential Improvements**:
- Transition from prototype boards to fully custom PCBs for better durability and compactness.
- Include dedicated connectors for easier and faster assembly.
- Integrate debugging points on the PCB to simplify troubleshooting.

### Circuit diagram 
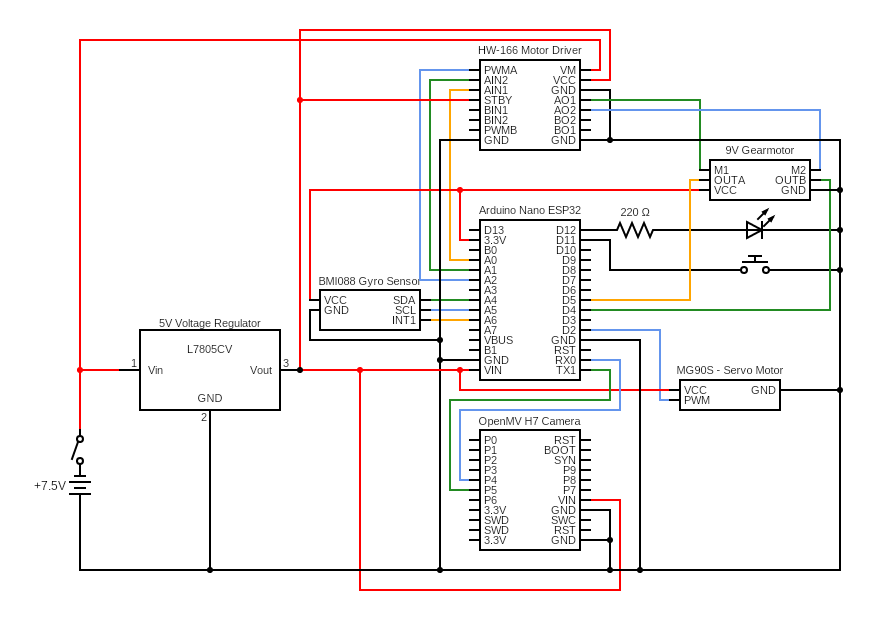
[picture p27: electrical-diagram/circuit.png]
Circuit diagram


<br>

# Code for each component 

## Drive Motor 

The motor driver can be directly managed with a single PWM pin that adjusts the motor's speed and two digital pins designated for determining the motor's rotation direction. Consequently, the use of any external library for motor manipulation was unnecessary.

We devised two functions within our control system: one to modify the motor's velocity and another to halt it effectively, incorporating a braking feature. To achieve this, we convert the desired speed from our established scale of -100 to +100 to the PWM equivalent of 0 to 1023. The motor's direction is then adjusted according to the sign of the input value.

Given the fact that the Arduino has an ESP chip, the PWM signals have to be sent using the ```ledc``` utility.

```ino
void motor_driver_setup() {
  ledcSetup(DRIVER_PWM_CHANNEL, PWM_FREQ, PWM_RES);
  ledcAttachPin(PWMA, DRIVER_PWM_CHANNEL);

  pinMode(AIN1, OUTPUT);
  pinMode(AIN2, OUTPUT);
}

void move_motor(double speed) {  // move the motor with a given speed in the [-100, 100] interval
  int dir = 1;
  if (speed < 0) {
    dir = -1;
    speed *= -1;
  }
  else if (speed == 0) {
    dir = 0;
  }
  speed = map_double(speed, 0, 100, 0, 1023);
  if (dir == 1) { // move the motor forward
    digitalWrite(AIN1, HIGH);
    digitalWrite(AIN2, LOW);
  }
  else if (dir == -1) { // move it backwards
    digitalWrite(AIN1, LOW);
    digitalWrite(AIN2, HIGH);
  }
  else { // implement active break (not used since we don't know how reliable it is)
    digitalWrite(AIN1, LOW);
    digitalWrite(AIN2, LOW);
  }
  ledcWrite(DRIVER_PWM_CHANNEL, (int)speed); // write the speed using PWM
}

void motor_break(long long break_time) { // stop the robot for a given time
  move_motor(-3);
  custom_delay(break_time);
}
```

However, for the encoder, we required a specialized library to handle the more complex signal processing. The library we use for interfacing with the encoder is called ```Encoder.h```.

The encoder operates with a straightforward function that we found easy to comprehend and program. In order to determine the distance in cm, we divided the returned value by 12, since the encoder measures 12 counts per revolution. Then we multiplied this with the gear ratio, wheel diameter and Pi. After that we divided by 10 to convert to cm.

Because of the way the ESP32 chip interacts with the components, in order for this library to properly work, we should select the pin numbering option as "by GPIO number", not as the default "by Arduino pin".

```ino
double read_motor_cm() {  // getting the distance driven by the motor in cm
  return GEAR_RATIO * WHEEL_DIAM * M_PI * (double)myEnc.read() / 12 / 10;
}
```

## Servo Motor 

For controlling the servo motor, we utilize the ```Servo.h``` library, which provides the necessary functions to manage the servo's movements. Initially, we configure the servo by establishing its range, defining the maximum and minimum angles it can achieve in both directions. This ensures that we can accurately position the servo within its operational limits.

```ino
void servo_setup() {
  // attach the servo to the right pin and move it to the minimum and maximum angles
  // in the end, center the servo so that we start the program moving straight
  servo.attach(SERVO_PIN);
  for (int deg = servo.read() - 1; deg >= ANGLE_MIN; deg--)
    servo.write(deg);
  custom_delay(500);
  // Serial.println("after ANGLE_MIN");
  for (int deg = servo.read() + 1; deg <= ANGLE_MID; deg++)
    servo.write(deg);
  // Serial.println("after ANGLE_MID");
  for (int deg = servo.read() + 1; deg <= ANGLE_MAX; deg++)
    servo.write(deg);
  custom_delay(500);
  // Serial.println("after ANGLE_MAX");
  for (int deg = servo.read() - 1; deg >= ANGLE_MID; deg--)
    servo.write(deg);
  custom_delay(500);
  // Serial.println("after ANGLE_MID");
  goal_deg = ANGLE_MID;
  custom_delay(2000); // some time to get rid of any unwanted movements so we don't disturb the gyro
}
```

The servo motor is controlled dinamically in the loop by setting a goal angle and taking small steps towards that goal at every iteration. This way we make sure that we can send a lot of fast angle changes to the servo and get the wanted results.

The function ```move_servo``` sets the goal angle to the given parameter. If the angle is negative the motor will rotate to the right, and if it is positive, the motor will rotate to left. This way, 0 is going to be the position in which the wheels are straight. Also, the values given the motor need to be between -1 and 1, so we use a clamp function to limit the value we are going to give the motor to rotate to and an interval mapping function to map the parameter from the [-1; 1] interval to the [ANGLE_MIN; ANGLE_MAX] interval.

The function ```update_servo``` takes a small step towards the goal angle as described above.

```ino
void move_servo(double angle) {  // move the servo to the angle checkpoint by setting the goal degrees to the angle value
  goal_deg = map_double(angle, -1, 1, ANGLE_MIN, ANGLE_MAX);
}

void update_servo() { // update the servo, making it closer to the goal angle by a small step
  int current_angle_servo = servo.read();
  if (abs(current_angle_servo - goal_deg) >= ANGLE_VARIANCE_THRESHOLD) { // if we're too far off, directly write the new angle
    servo.write(goal_deg);
  }
  else {
    // increment the angle with a small step in the right direction
    // making sure we don't exceed our angle limitations
    if (current_angle_servo < goal_deg) {
      servo.write(min(current_angle_servo + STEP, ANGLE_MAX));
    }
    else if (current_angle_servo > goal_deg) {
      servo.write(max(current_angle_servo - STEP, ANGLE_MIN));
    }
  }
}

void loop() {
  // other code
  update_servo();
}
```

## Camera 

Now that we finished implementing the functions that we need to make the robot move and steer, we have to make it see the lines that trigger the turns, the cubes and the parking walls and move accordingly. To communicate with the camera, we use the ```UART``` protocol. In order for this to work, we must link the ```RX0``` pin on the arduino (the receiver pin) to the ```P4``` pin on the camera (the transmitter pin) and the ```TX1``` pin on the arduino (the transmitter pin) to the ```P5``` pin on the camera (the receiver pin). In addition, the baud rates from the ```Serial0``` object on the arduino and the ```uart``` object on the camera must match.

**Arduino code:**

```ino
void comm_setup() {
  Serial.begin(9600);
  // while(!Serial);
  blink_led(LED_BUILTIN, 500);

  Serial0.begin(19200);
  while(!Serial0); // wait for the serial to properly initialize
  blink_led(LED_BUILTIN, 500);
  receivedMessage = "";
}

void loop() {
  // execute pending commands
  while (Serial0.available() > 0) { // if we have some characters waiting
    char receivedChar = Serial0.read(); // we get the first character
    if (receivedChar == '\n') { // if it's the end of message marker
      if (CASE != PARK) { // if we want to execute commands
        execute(receivedMessage); // execute the received command from the OpenMV camera
      }
      receivedMessage = ""; // reset the received message
    }
    else {
      receivedMessage += receivedChar; // append characters to the received message
    }
  }
}
```

**Camera code:**

```py
# setup UART connection to arduino
uart = UART(3, 19200)
# 3 - the uart config, meaning that we use pins P4 as the transmitter, P5 as the receiver
# 19200 - baud rate aka frequency, must match the one set up on the arduino

# because we have a one-sided communication going on
# we can directly write messages without any supplementary checks
uart.write(msg)
```

In order to detect colors, we have to take pictures in which to search for colors. This is the sequence that sets up the camera sensor. Due to the limitations of the sensor, we couldn't manually adjust the white balance, gain, exposure time or access its registries.

```py
import sensor

# initialize the sensor
sensor.reset()
sensor.set_pixformat(sensor.RGB565)
sensor.set_framesize(sensor.QQVGA)
#sensor.set_framerate(40)
sensor.set_vflip(True)
sensor.set_hmirror(True)

# disable auto gain, white balance, and exposure
sensor.set_auto_gain(False)  # must be turned off for color tracking
sensor.set_auto_whitebal(False)  # must be turned off for color tracking
sensor.set_auto_exposure(False, exposure_us=10000) # set constant exposure for the best visibility

# skip some frames to let the camera adjust
sensor.skip_frames(time=2000)
```

Now for the camera logic, the color tracking is pretty simple: the camera can return blobs of pixels that fit into a certain ```LAB``` threshold representing a color. We can also restrain the blob detection to a rectangle of interest and apply pixel count, bounding rectangle area and density filters as well. The reason for which we do this, is that certain colors, like green, red, blue and orange are pretty common, therefore we don't want the camera to interpret clothes or other objects outside of the map as obstacles. In addition, the orange and red colors, in some light conditions, are quite similar. This is why we apply the pixel count, bounding rectangle area and density filters, to ensure that we are seeing the correct object.

For quali we firstly scan the color of the first seen line. This will give us the direction of the run. Then, we constantly look out for lines that are over a certain area. Once we find one, we send the turn trigger to the Arduino via ```UART```.

```py
while (True):
    clock.tick()
    img = sensor.snapshot()

    # find the coloured blobs corresponding to the turn lines
    orange_blobs = img.find_blobs(orange_threshold, roi=lines_roi, pixels_threshold=line_blob_size, area_threshold=line_blob_size, merge=True)
    blue_blobs = img.find_blobs(blue_threshold, roi=lines_roi, pixels_threshold=line_blob_size, area_threshold=line_blob_size, merge=True)

    orange_blob_w = None
    orange_blob_h = None
    max_width = 0
    max_height = 0
    for blob in orange_blobs:
        if blob.w() >= img.width() * 0.4: # if it meets the minimum width requirement
            if blob.w() > max_width: # if it's the biggest blob yet
                max_width = blob.w()
                orange_blob_w = blob # biggest blob on the width
        if blob.h() >= lines_roi[3] * 0.4: # if it meets the minimum height requirement
            if blob.h() > max_height: # if it's the biggest blob yet
                max_height = blob.h()
                orange_blob_h = blob # biggest blob on the height
    # if we have a blob meeting either the minimum width or height requirement we remember it
    orange_blob = orange_blob_w
    if not orange_blob:
        orange_blob = orange_blob_h

    blue_blob_w = None
    blue_blob_h = None
    max_width = 0
    max_height = 0
    for blob in blue_blobs:
        if blob.w() >= img.width() * 0.4: # if it meets the minimum width requirement
            if blob.w() > max_width: # if it's the biggest blob yet
                max_width = blob.w()
                blue_blob_w = blob # biggest blob on the width
        if blob.h() >= lines_roi[3] * 0.4: # if it meets the minimum height requirement
            if blob.h() > max_height: # if it's the biggest blob yet
                max_height = blob.h()
                blue_blob_h = blob # biggest blob on the height
    # if we have a blob meeting either the minimum width or height requirement we remember it
    blue_blob = blue_blob_w
    if not blue_blob:
        blue_blob = blue_blob_h

    if direction == 0: # if we didn't set a turn direction yet
        if orange_blob: # if the first line we saw was an orange one
            direction = 2
        elif blue_blob: # if the first line we saw was a blue one
            direction = 1

    has_line = False
    if orange_blob or blue_blob: # if we saw either coloured lines, we can make a turn
        has_line = True

    if has_line:
        # if we must turn, send the turn trigger
        uart.write(str(direction) + '\n')
```

## IMU 

To utilize the gyro sensor, we needed to include the ```BMI088.h``` library. During initialization, we allocate a 10-second window to measure the sensor's drift, allowing us to refine the robot's angular readings for greater precision. Additionally, we configure the sensor's output data rate to 400Hz and set the bandwidth to 47Hz. The bandwidth determines the frequency of data sampling by the sensor; a higher bandwidth yields more precise data at the cost of increased power consumption. We also designate pin A6 as an input and attach an interrupt to it, enabling us to capture data from the sensor as soon as it becomes available.

```ino
void gyro_setup(bool debug) {
  int status = accel.begin();
  status = accel.setOdr(Bmi088Accel::ODR_200HZ_BW_80HZ);
  status = accel.pinModeInt1(Bmi088Accel::PUSH_PULL,Bmi088Accel::ACTIVE_HIGH);
  status = accel.mapDrdyInt1(true);

  status = gyro.begin();

  status = gyro.setOdr(Bmi088Gyro::ODR_400HZ_BW_47HZ);
  status = gyro.pinModeInt3(Bmi088Gyro::PUSH_PULL,Bmi088Gyro::ACTIVE_HIGH);
  status = gyro.mapDrdyInt3(true);

  pinMode(INT_PIN,INPUT);
  attachInterrupt(INT_PIN,gyro_drdy,RISING);

  if(status < 0) {
    if(debug){
      Serial.print("BMI Initialization Error!  error: ");
      Serial.println(status);
    }
  }
  else  {
    // Gyro drift calculation
    if(debug) Serial.println("Starting gyro drift calculation...");

    gx = 0;
    // gy = 0;
    // gz = 0;

    gyro_last_read_time = millis();

    double start_time = millis();
    while(millis() - start_time < DRIFT_TEST_TIME * 1000) {
      gyro.readSensor();
      double read_time = millis();
      gx += (gyro.getGyroX_rads() * (read_time - gyro_last_read_time) * 0.001);
      // gy += (gyro.getGyroY_rads() * (read_time - gyro_last_read_time) * 0.001);
      // gz += (gyro.getGyroZ_rads() * (read_time - gyro_last_read_time) * 0.001);

      gyro_last_read_time = read_time;
    }

    drifts_x = gx / DRIFT_TEST_TIME;
    // drifts_y = gy / DRIFT_TEST_TIME;
    // drifts_z = gz / DRIFT_TEST_TIME;

    if(debug) Serial.print("Drift test done!\nx: ");
    if(debug) Serial.println(drifts_x, 6);
    // if(debug) Serial.print("   y: ");
    // if(debug) Serial.print(drifts_y, 6);
    // if(debug) Serial.print("   z: ");
    // if(debug) Serial.println(drifts_z, 6);
  }
  // Gyro value reset
  gx = 0;
  // gy = 0;
  // gz = 0;

  gyro_last_read_time = millis();
}
```

Within the ```read_gyro``` function, we're retrieving data from the gyro sensor and adjusting it to account for any detected drift, enhancing the accuracy of the readings. Since the gyro provides data in radians, a conversion to degrees is necessary for our application. We're focusing solely on the rotation around the x-axis, hence we only compute the ```gx``` value, which represents the robot's angular rotation in degrees on that specific axis.

```ino
void read_gyro(bool debug) {
  if(gyro_flag) {
    gyro_flag = false;
    gyro.readSensor();   
    double read_time = millis();

    gx += ((gyro.getGyroX_rads() - drifts_x) * (read_time - gyro_last_read_time) * 0.001) * 180.0 / PI;
    // gy += ((gyro.getGyroY_rads() - drifts_y) * (read_time - gyro_last_read_time) * 0.001) * 180.0 / PI;
    // gz += ((gyro.getGyroZ_rads() - drifts_z) * (read_time - gyro_last_read_time) * 0.001) * 180.0 / PI;

    gyro_last_read_time = read_time;

    if(debug) {
      Serial.print("Gyro: gx: ");
      Serial.println(gx);
      // Serial.print(" gy: ");
      // Serial.print(gy);
      // Serial.print(" gz: ");
      // Serial.println(gz);
    }
  }
}
```

<br>

# Obstacle Management 

## Qualification Round 

For the qualifying round, we set up a basic switch-case system to guide our robot. This system tells the robot what to do next, depending on where it is. The robot knows where it is by counting how many times it has turned.

We use two main switch cases: ```PID``` and ```STOP_QUALI```.

In the ```PID``` case, the robot moves straight and turns. It uses a special tool (PID controller) with a gyro sensor to stay on a straight line. If it sees a corner line, it gets a trigger from the camera to make a turn by adding 90 degrees to the goal angle.

```ino
case PID: {
  double err = current_angle_gyro - gx;
  if (millis() - last_rotate > FIRST_STOP_DELAY && turns >= 12) { // if we did 3 runs of the round
    if (FINAL) {
      CASE = STOP_BEFORE_FIND_PARKING; // we need to stop and search for the parking
    }
    else {
      CASE = STOP_QUALI; // stop, challenge over
    }
  }
  else {
    // classic pid on the gyro so that we can move straight
    pid_error_gyro = (err) * kp_gyro + (pid_error_gyro - pid_last_error_gyro) * kd_gyro;
    pid_last_error_gyro = pid_error_gyro;
    move_servo(pid_error_gyro);
  }
  move_motor(MOTOR_SPEED);
  break;
}

case STOP_QUALI: {
  // we finished the challenge, stop the robot
  move_until_angle(MOTOR_SPEED, current_angle_gyro);
  move_cm_gyro(10, MOTOR_SPEED, current_angle_gyro);
  is_running = false;
  Serial.println("Stop case");
  motor_break(1000000000);
}
```

### Line Detection
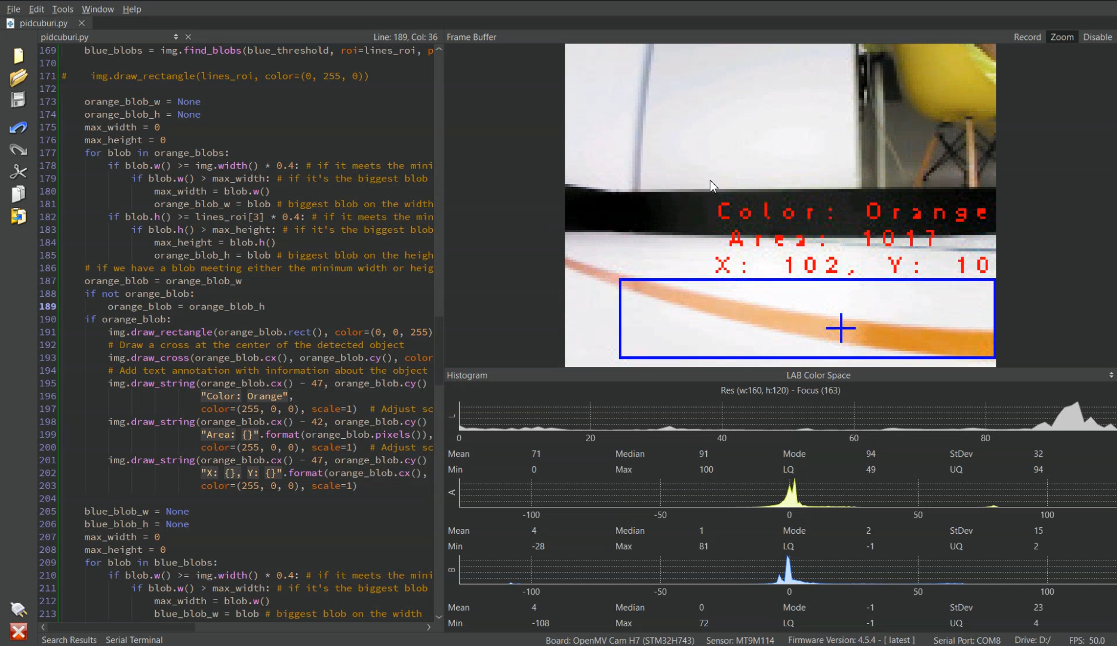
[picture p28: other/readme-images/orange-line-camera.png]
Line Detection


## Final Round 

For the final round, we based our controller algorithm on the quali code, adding a PID controller on the camera to follow the closest cube until it is in its proximity. In order to get the closest cube to the robot we just search for the biggest red or green coloured blob in the image.
After we're in the cube's proximity, we send a trigger from the camera to the arduino with the cube color so that we can start avoiding it.

```py
img = sensor.snapshot()

# find the coloured blobs corresponding to the cubes
red_blobs = img.find_blobs(red_threshold, roi=cubes_roi, pixels_threshold=min_cube_size, area_threshold=min_cube_size, merge=True)
green_blobs = img.find_blobs(green_threshold, roi=cubes_roi, pixels_threshold=min_cube_size, area_threshold=min_cube_size, merge=True)

msg = "0\n"
max_area = 0
color = 'none'
saved_cube = None
for blob in red_blobs: # for every red blob
    # if they're passing the height and density filters
    # we're keeping the biggest one and its color
    if is_cube(blob, orange_blob, parking_blobs) and blob.area() > max_area:
        max_area = blob.area()
        saved_cube = blob
        color = 'red'
for blob in green_blobs: # for every green blob
    # if they're passing the height and density filters
    # we're keeping the biggest one and its color
    if is_cube(blob, blue_blob, parking_blobs) and blob.area() > max_area:
        max_area = blob.area()
        saved_cube = blob
        color = 'green'

if saved_cube != None: # if we saw a cube
    # if the cube area is over a certain threshold
    # it means we must avoid the cube as we are too close to it
    if saved_cube.h() >= max_cube_height:
        # send the right trigger
        err_old = 0
        if color == 'red':
            uart.write('R\n')
        else:
            uart.write('G\n')
        if has_line:
            # if we must also turn, send the trigger
            uart.write(str(direction) + '\n') # send the turn trigger
    else: # if the cube isn't too big we must follow it
        # calculate the angle using PID
        err = saved_cube.cx() - img.width() / 2
        steering = err * kp + (err - err_old) * kd
        steering = -clamp(steering, -1, 1)
        err_old = err
        # craft the command
        if color == 'red':
            msg = 'r' + str(steering) + '\n'
        else:
            msg = 'g' + str(steering) + '\n'
        uart.write(msg) # send the message
        if has_line:
            # if we must also turn, send the turn trigger
            uart.write(str(direction) + '\n')
elif has_line: # if we don't see any cubes
    uart.write(str(direction) + '\n')
```

### Cube Detection
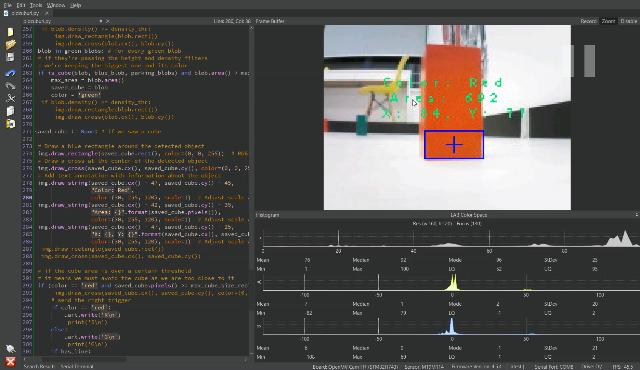
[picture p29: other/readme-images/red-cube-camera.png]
Red Cube Detection

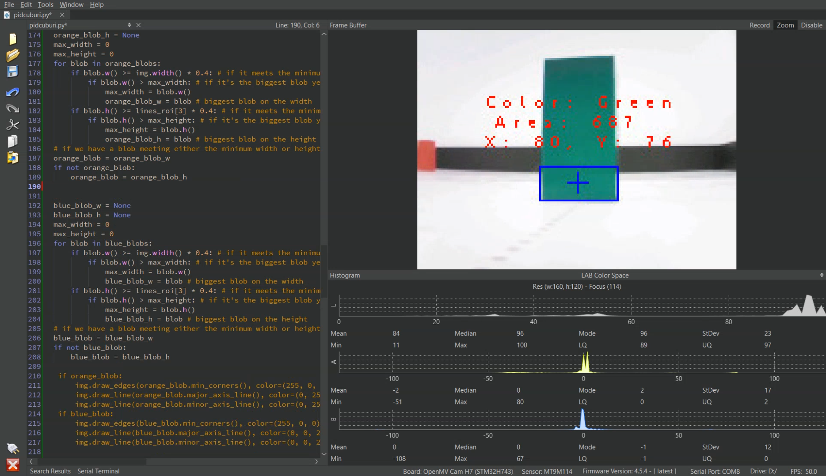
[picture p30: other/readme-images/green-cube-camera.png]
Green Cube Detection


---

The arduino part is quite simple, consisting of the quali switch but with two extra cases: ```FOLLOW_CUBE``` and ```AFTER_CUBE```. In the ```FOLLOW_CUBE``` case we just write to the servo the steering angle calculated by the PID algorithm ran on the camera. After we get the proximity trigger from the camera, we have a custom function called ```pass_cube``` which steers us away from the cube and puts us in the ```AFTER_CUBE``` state. This case consists of two substates: in the first one the robot steers in the opposite direction to center itself again and the second one in which the robot uses a PID with the gyro to move an additional distance so that we're perfectly positioned to see the next cube. After that, we go back to the default ```PID``` case that is used in the quali code.

```ino
// hardcoded sequence that avoids a cube
void pass_cube(int cube_last) {
  read_gyro(false);
  double angle_addition = 0;
  double start_angle = gx;
  double err = abs(current_angle_gyro - start_angle);

  if (err >= 50) { // if we're really crooked, substract a given value so that we don't overcompensate
    angle_addition -= 10;
  }
  else {
    angle_addition -= max(err / 2.75, 0.0); // if we're crooked, dinamically adjust the avoidance angle so that we don't overshoot
  }
  move_until_angle(MOTOR_SPEED, start_angle - cube_last * (AVOIDANCE_ANGLE + angle_addition)); // steer away from the cube
  start_angle = gx;

  last_cube_time = millis();
  CASE = AFTER_CUBE;
}
```

```ino
case FOLLOW_CUBE: {
  if (millis() - last_rotate > FIRST_STOP_DELAY && turns >= 12) { // if we did 3 runs of the obstacle round, we need to stop and search for the parking
    CASE = STOP_BEFORE_FIND_PARKING;
  }
  else {
    if (millis() - last_follow_cube > FOLLOW_CUBE_DEAD_TIME) // if we lost the cube, we just go back to the default PID case
      CASE = PID;
    // write to the servo the pid computed on the camera in order to follow the cube
    move_servo(follow_cube_angle);
    move_motor(MOTOR_SPEED);
  }
  break;
}

case AFTER_CUBE: {
  if (millis() - last_rotate > FIRST_STOP_DELAY && turns >= 12) { // if we did 3 runs of the obstacle round, we need to stop and search for the parking
    CASE = STOP_BEFORE_FIND_PARKING;
  }
  else {
    int angle_addition = 0;
    if (cube_last == 1) // due to a slight asymmetry in the steering, when avoiding red cubes we need to steer less
      angle_addition = -9;
    double err = current_angle_gyro - gx + cube_last * (CORRECTION_ANGLE + angle_addition);
    if (abs(err) < 5) {
      // after we avoid the cube, move forward a bit more so that we're positioned
      // to see the next cube
      if (cube_last == turn_direction) // compensate less on the inside
        move_cm_gyro(5, MOTOR_SPEED, current_angle_gyro + cube_last * (CORRECTION_ANGLE + angle_addition));
      else
        move_cm_gyro(10, MOTOR_SPEED, current_angle_gyro + cube_last * (CORRECTION_ANGLE + angle_addition));
      CASE = PID;
    }
    else {
      // classic pid on the gyro so that we can move in the opposite direction
      // so that we can see the next cube
      pid_error_gyro = (err) * kp_gyro + (pid_error_gyro - pid_last_error_gyro) * kd_gyro;
      pid_last_error_gyro = pid_error_gyro;
      move_servo(pid_error_gyro);
    }
  }
  move_motor(MOTOR_SPEED);
  break;
}
```

The next challenge in this round consists in the final turnaround. If the last seen cube is red, we need to do a roundabout and complete the last lap in the opposite direction. The way we deal with this is an ```if``` condition that gets executed before we pass a cube. The turn condition is simple: if we did the required number of turns and if we're either right after a turn and the last avoided cube is red or if we're further away from the turn and the cube we want to avoid now is red then we turn around.

```ino
void execute() {
  if ((cmd[0] == 'R' || cmd[0] == 'G') && millis() - last_cube_time >= PASS_CUBE_DELAY) { // if we're in the proximity of a cube
    before_side_last_cube = cube_last; // remember the last passed cube (excluding this one)
    if (cmd[0] == 'R') { // we determine the direction in which we avoid the cube and remember its color
      cube_last = 1;
    }
    else {
      cube_last = -1;
    }

    if (turns == 8 && ((cube_last == 1 && millis() - last_rotate < TURNAROUND_DELAY) || millis() - last_rotate > TURNAROUND_DELAY && before_side_last_cube == 1) && !turned) // if we have are in the position to turn around, the cube is red and we haven't turned around already
      turn_around(cube_last);
    else 
      pass_cube(cube_last);
    return;
  }
}

// hardcoded sequence that turns around
// we need the last passed cube so that we know which way we take the turn so that we don't hit anything
void turn_around(int cube_last) {
  read_gyro(false);
  double start_angle = gx;
  move_until_angle(MOTOR_SPEED, start_angle - cube_last * 57);
  move_until_angle(MOTOR_SPEED, current_angle_gyro + cube_last * 200);
  current_angle_gyro += cube_last * 180;
  turn_direction *= -1;
  turned = true;
  CASE = PID;
}
```

The final challenge in this round consists in parking the robot. The way we implement this is based on the quali. Basically we want to move as close to the outer walls as possible so that we're perfectly positioned for the parking and avoid all of the cubes. How we achieve this is by going perpendicular to the outside walls after we finish the obstacle round (see the ```POSITION_BEFORE_FIND_PARKING``` case). The goal is to position ourselves as close as possible to them. After we receive a trigger from the camera saying that we're in its proximity, we straighten ourselves out and start the basic quali code.

While moving around the map like this (in the ```FIND_PARKING``` case), we are constantly scanning for magenta blobs that represent the parking walls. When we detect them, we send a trigger from the camera to the arduino and then we have a hardcoded sequence that puts us between the walls, perfectly parallel to them, implemented in the ```POSITION_FOR_PARK``` case. After that, we move straight in order to get closer to the outer wall (see the ```PARK``` case). When we receive the trigger from the camera, position ourselves and stop the robot.

Camera code:

```py
# checks if a parking wall blob meets the height and size requirements
def is_parking_wall(blob):
    if not blob:
        return False
    if blob.pixels() >= parking_blob_size_trigger and blob.area() >= parking_blob_size_trigger and blob.h() >= parking_blob_height_trigger:
        return True
    return False

img = sensor.snapshot()

# find the coloured blobs corresponding to the parking walls
parking_blobs = img.find_blobs(parking_threshold, roi=parking_roi, pixels_threshold=parking_blob_size_min, area_threshold=parking_blob_size_min, merge=True)
parking_wall_blob = get_biggest_blob(parking_blobs)

# find the coloured blobs corresponding to the outside walls
wall_blobs = img.find_blobs(black_threshold, roi=wall_roi, pixels_threshold=wall_blob_size, area_threshold=wall_blob_size, merge=True)
outer_wall = get_biggest_blob(wall_blobs)

gray_img = img.copy()  # make a copy of the image
gray_img.to_grayscale()  # convert to grayscale

# determine the brightness of the ROIs to know if we're close to an outside wall or not
left_dark_pixels = 0
right_dark_pixels = 0
middle_dark_pixels = 0

# process pixels in the left ROI
for y in range(wall_dark_roi[1], wall_dark_roi[1] + wall_dark_roi[3]):
    for x in range(wall_dark_roi[0], wall_dark_roi[0] + wall_dark_roi[2]):
        if gray_img.get_pixel(x, y) < dark_threshold:
            middle_dark_pixels += 1

# process pixels in the left ROI
for y in range(wall_left_roi[1], wall_left_roi[1] + wall_left_roi[3]):
    for x in range(wall_left_roi[0], wall_left_roi[0] + wall_left_roi[2]):
        if gray_img.get_pixel(x, y) < dark_threshold:
            left_dark_pixels += 1

# process right ROI
for y in range(wall_right_roi[1], wall_right_roi[1] + wall_right_roi[3]):
    for x in range(wall_right_roi[0], wall_right_roi[0] + wall_right_roi[2]):
        if gray_img.get_pixel(x, y) < dark_threshold:
            right_dark_pixels += 1

# calculate darkness percentages
left_total_pixels = wall_left_roi[2] * wall_left_roi[3]
right_total_pixels = wall_right_roi[2] * wall_right_roi[3]
middle_total_pixels = wall_dark_roi[2] * wall_dark_roi[3]

left_dark_percentage = (left_dark_pixels / left_total_pixels) * 100
right_dark_percentage = (right_dark_pixels / right_total_pixels) * 100
middle_dark_percentage = (middle_dark_pixels / middle_total_pixels) * 100

if is_parking_wall(parking_wall_blob):
    # if we saw the parking walls, send the parking trigger
    uart.write('P\n')
if wall_blobs:
    # if the wall is big enough, send a slightly different message that helps us when parking
    # if not, send the classic one
    if middle_dark_percentage > 75:
        uart.write('WP\n')
    else:
        uart.write('W\n')
```

### Parking Wall Detection
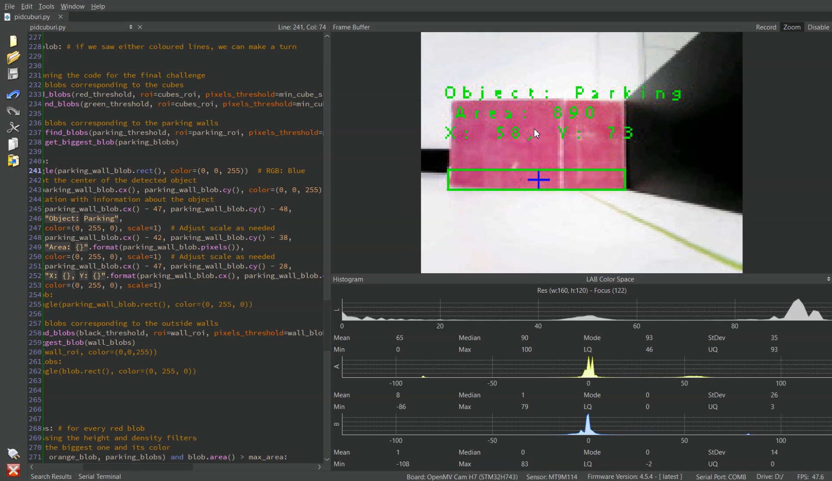
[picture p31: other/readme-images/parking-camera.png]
Parking Wall Detection


---

**Arduino code:**

```ino
case STOP_BEFORE_FIND_PARKING: {
  // straighten ourselves, start positioning for the parking
  move_cm_gyro(22, MOTOR_SPEED, current_angle_gyro);
  motor_break(1000);
  CASE = POSITION_BEFORE_FIND_PARKING;
  break;
}

case POSITION_BEFORE_FIND_PARKING: {
  // classic pid on the gyro so that we can move perpendicular to the walls
  // we don't just call the move_until_angle function so that we can still execute commands
  double err = current_angle_gyro - gx - turn_direction * 90;
  pid_error_gyro = (err) * kp_gyro + (pid_error_gyro - pid_last_error_gyro) * kd_gyro;
  pid_last_error_gyro = pid_error_gyro;
  move_servo(pid_error_gyro);
  move_motor(MOTOR_SPEED);
  break;
}

case FIND_PARKING: {
  // classic pid on the gyro so that we can move straight
  // basically immitating a quali run until we find the parking spot
  double err = current_angle_gyro - gx;
  pid_error_gyro = (err) * kp_gyro + (pid_error_gyro - pid_last_error_gyro) * kd_gyro;
  pid_last_error_gyro = pid_error_gyro;
  move_servo(pid_error_gyro);
  move_motor(MOTOR_SPEED);
  break;
}

case POSITION_FOR_PARK: {
  // hardcoded sequence of moves that positions us in the parking spot
  // after that, we just get closer to the outside wall so that we're fully in
  move_cm_gyro(16, PARKING_SPEED, current_angle_gyro);
  drift(PARKING_SPEED, turn_direction, current_angle_gyro + turn_direction * 90);
  move_cm_gyro(10, -PARKING_SPEED, current_angle_gyro + turn_direction * 90);
  drift(PARKING_SPEED, -turn_direction, current_angle_gyro - turn_direction * 90);
  CASE = PARK;
  break;
}

case PARK: {
  // classic pid on the gyro so that we can move straight into the parking space
  // we don't just call the move_until_angle function so that we can still execute commands
  double err = current_angle_gyro - gx - turn_direction * 90;
  pid_error_gyro = (err) * kp_gyro + (pid_error_gyro - pid_last_error_gyro) * kd_gyro;
  pid_last_error_gyro = pid_error_gyro;
  move_servo(pid_error_gyro);
  move_motor(PARKING_SPEED);
  break;
}

case STOP_FINAL: {
  // we finished the challenge, stop the robot
  is_running = false;
  Serial.println("Stop case");
  motor_break(1000000000);
}
```

## Additional code 

**Arduino code:**

In order to clean up the code, we designed some additional functions. Whenever we want to call locomotion functions or delay functions, functions that would break the continuity of the loop function, we must do two things to make sure everything keeps working: flush the characters sent by the camera (using the ```flush_messages``` function) and read the gyro data. That's why we implemented a custom delay function and our locomotion functions are a bit atypical.

```ino
void flush_messages() { // flushing messages like this so that we don't get sections of messages
  // improves the stability of the communication
  while (Serial0.available() > 0) { // if we have some characters waiting
    char receivedChar = Serial0.read(); // we get the first character
    if (receivedChar == '\n') { // if it's the end of message marker
      receivedMessage = ""; // reset the received message
    }
    else {
      receivedMessage += receivedChar; // append characters to the received message
    }
  }
}

void custom_delay(long long delay_time) { // delay function that flushes all of the data
  long long start_time = millis();
  while (millis() - start_time < delay_time) {
    read_gyro(false);
    flush_messages();
  }
}
```

Functions used for locomotion:
```ino
// makes the robot move until it reaches a certain gyro angle
void move_until_angle(double speed, double gyro_offset) {
  int sign = 1;
  if (speed < 0) // if we're moving backwards, we need to steer in the opposite direction
    sign = -1;
  read_gyro(false);
  double err = gyro_offset - gx;
  while (abs(err) >= 10) { // while the error is too big
    // pid on the gyro so that we're moving towards the goal angle
    read_gyro(false);
    err = gyro_offset - gx;
    pid_error_gyro = (err) * kp_gyro + (pid_error_gyro - pid_last_error_gyro) * kd_gyro;
    pid_last_error_gyro = pid_error_gyro;
    move_servo(pid_error_gyro * sign);
    update_servo();
    move_motor(speed);
    flush_messages();
  }
}

// makes the robot move a certain distance at a certain gyro angle
void move_cm_gyro(double dis, double speed, double gyro_offset) {
  double start_cm = read_motor_cm();
  int sign = 1;
  if (speed < 0) // if we're moving backwards, we need to steer in the opposite direction
    sign = -1;
  while (abs(read_motor_cm() - start_cm) < dis) { // while we haven't moved the requested distance
    // pid on the gyro so that we're moving at the correct angle
    read_gyro(false);
    double err = gyro_offset - gx;
    pid_error_gyro = (err) * kp_gyro + (pid_error_gyro - pid_last_error_gyro) * kd_gyro;
    pid_last_error_gyro = pid_error_gyro;
    move_servo(pid_error_gyro * sign);
    update_servo();
    move_motor(speed);
    flush_messages();
  }
}

// makes the robot move at a certain steering angle until it reaches a certain gyro angle
void drift(double speed, double steering, double gyro_offset) {
  read_gyro(false);
  double err = gyro_offset - gx;
  while (abs(err) >= 10) { // while the error is too big
    read_gyro(false);
    err = gyro_offset - gx;
    move_servo(steering);
    update_servo();
    move_motor(speed);
    flush_messages();
  }
}
```

Lastly, we receive multiple types of commands from the camera, from different triggers, to cube following and avoiding commands. All of these take various forms, therefore we need a function that parses every command and executes it. This is where the ```execute``` and ```valid_command``` functions come in handy. The ```execute``` function executes the command only if the ```valid_command``` function says it's valid.

```ino
bool valid_command(String cmd) { // function that checks the validity of a command received from the camera
  if (cmd == "")
    return false;
  if ('0' <= cmd[0] && cmd[0] <= '9') {
    if (cmd[0] > '2' || cmd[0] == '0')
      return false;
    if (cmd.length() != 1)
      return false;
  }
  if (cmd[0] == '+' || cmd[0] == '-' || cmd[0] == '.')
    return false;
  return true;
}

// function that parses a command and executes it
void execute(String cmd) {
  if (!valid_command(cmd))
    return;

  // the following sequence gets the number from the command (if available)
  int pos = 0, sign = 1;
  if (cmd[pos] == 'r' || cmd[pos] == 'g')
    pos++;
  // manually going over the signs since the .toDouble function wouldn't parse them on its own
  if (cmd[pos] == '+')
    sign = 1, pos++;
  else if (cmd[pos] == '-')
    sign = -1, pos++;
  double val = cmd.substring(pos).toDouble();

  if (FINAL) { // if we're in the final round
    if (CASE == FIND_PARKING && cmd[0] == 'P') { // if we're searching for the parking spot and we find it
      CASE = POSITION_FOR_PARK; // park the robot
      return;
    }

    if (cmd[0] == 'P') // if we see the parking slot, but we didn't finish the obstacle round we ignore it
      return;

    if (CASE == POSITION_BEFORE_FIND_PARKING && cmd[0] == 'W') { // if we're positioning ourselves close to the wall and we're in its proximity
      move_until_angle(MOTOR_SPEED, current_angle_gyro); // straighten ourselves
      CASE = FIND_PARKING; // start searching for the parking lot
      return;
    }

    if (CASE == PARK && (cmd[0] == 'W' && cmd[1] == 'P')) { // if we're positioning ourselves close to the wall and we're in its proximity
      // move_cm_gyro(2.75, PARKING_SPEED, current_angle_gyro - turn_direction * 90); // position ourselves closer
      CASE = STOP_FINAL; // we finished the parking, stop
      return;
    }

    if (cmd[0] == 'W') // if we see the outer wall, but we don't need it we ignore it
      return;

    if (CASE != FIND_PARKING && CASE != POSITION_BEFORE_FIND_PARKING) {
      if ((cmd[0] == 'R' || cmd[0] == 'G') && millis() - last_cube_time >= PASS_CUBE_DELAY) { // if we're in the proximity of a cube
        before_side_last_cube = cube_last; // remember the last passed cube (excluding this one)
        if (cmd[0] == 'R') { // we determine the direction in which we avoid the cube and remember its color
          cube_last = 1;
        }
        else {
          cube_last = -1;
        }

        if (turns == 8 && ((cube_last == 1 && millis() - last_rotate < TURNAROUND_DELAY) || millis() - last_rotate > TURNAROUND_DELAY && before_side_last_cube == 1) && !turned) // if we have are in the position to turn around, the cube is red and we haven't turned around already
          turn_around(cube_last);
        else 
          pass_cube(cube_last);
        return;
      }
      if (cmd[0] == 'r' || cmd[0] == 'g') { // if we see a cube but we're not close enough to avoid it
        follow_cube_angle = val * sign;
        CASE = FOLLOW_CUBE;
        last_follow_cube = millis();
        return;
      }
    }
  }
  
  int msg = (int)val;
  if (msg) { // a turn was detected
    if (turn_direction == 0) { // if we don't know the direction yet
      if (msg == 1) { // blue line
        turn_direction = 1;
      }
      else { // orange line
        turn_direction = -1;
      }
    }
    if (millis() - last_rotate > delay_walls) { // if we can make a turn
      if (CASE == FIND_PARKING) { // if we're searching for the parking spot
        // if we're at the first turn, we have to move more in order to position ourselves close to the outer walls
        move_cm_gyro(CORNER_DISTANCE_PARKING, MOTOR_SPEED, current_angle_gyro);
      }
      else if (abs(current_angle_gyro - gx) < 10) { // if we're during the obstacle round or in the quali and we're straight
        // position ourselves in order to not hit the walls
        if (FINAL)
          move_cm_gyro(CORNER_DISTANCE_FINAL, MOTOR_SPEED, current_angle_gyro);
        else
          move_cm_gyro(CORNER_DISTANCE_QUALI, MOTOR_SPEED, current_angle_gyro);
      }
      else if (CASE == AFTER_CUBE) { // if we're crooked after avoiding a cube we position ourselves for the turn
        if (-cube_last == turn_direction) { // if we passed by it in the turn's direction then we just need to straighted ourselves for more manuver room
          move_until_angle(MOTOR_SPEED, current_angle_gyro);
        }
        else {
          move_until_angle(MOTOR_SPEED, current_angle_gyro + turn_direction * 30);
          move_cm_gyro(7, MOTOR_SPEED, current_angle_gyro + turn_direction * 30);
        }
        CASE = PID;
      }
      current_angle_gyro += turn_direction * 90; // update the goal angle for the next sequence
      turns++; // increase the number of turns made
      delay_walls = 2300; // larger delay for every turn except the first one
      // as we may have the starting position close to the first turn
      last_rotate = millis(); // update the last time we turned
    }
  }
}
```

**Camera code:**

In order to make the robot more stable in any light conditions, we had to make sure that the red, orange and magenta, respectively the green and the blue colors don't get confused in the color detection process. That's why in order to ensure the best accuracy we fine tuned our color thresholds so that we can never see magenta/orange on a red cube or blue on a green cube. The problem that remained is that we saw red in magenta/orange and green in blue. That's why we came up with a simple solution: if a red/green blob is inside another blob that can be mixed up with, such as a line blob or a parking wall blob, we simply ignore it, as it is a false cube detected.

```py
# detects if a blob is partially inside another blob
# by checking if the center of one blob is inside the minimum area rectangle that wraps the other blob
# giving the fact that this rectangle may be crooked, we have to use a special algorithm
# that is designed to check whether a point is inside a polygon or not based on the coordinates
def is_blob_in_blob(blob, blob2):
    if not blob2:
        return False
    polygon = blob2.min_corners()
    num_vertices = len(polygon)
    (x, y) = (blob.cx(), blob.cy())
    inside = False

    # store the first point in the polygon
    (p1x, p1y) = (polygon[0][0], polygon[0][1])

    # loop through each edge in the polygon
    for i in range(1, num_vertices + 1):
        # get the next point in the polygon
        (p2x, p2y) = (polygon[i % num_vertices][0], polygon[i % num_vertices][1])

        # check if the point is above the minimum y coordinate of the edge
        # check if the point is below the maximum y coordinate of the edge
        # check if the point is to the left of the maximum x coordinate of the edge
        if y > min(p1y, p2y) and y <= max(p1y, p2y) and x <= max(p1x, p2x):
            # calculate the x-intersection of the line connecting the point to the edge
            x_intersection = (y - p1y) * (p2x - p1x) / (p2y - p1y) + p1x

            # check if the point is on the same line as the edge or to the left of the x-intersection
            if p1x == p2x or x <= x_intersection:
                # flip the inside flag
                inside = not inside

        # store the current point as the first point for the next iteration
        (p1x, p1y) = (p2x, p2y)

    # return the value of the inside flag
    return inside

# checks whether a blob is a cube or not based on the minimum height and density filters
# as well as another check:
# since in some light conditions the red the cube may be similar to the orange line or magenta parking walls
# and in some light conditions the green the cube may be similar to the blue line
# we have to check if the possible cube blob is inside any of these ones
# if it is, then it may just be a false alarm and we should ignore it
def is_cube(blob, line_blob, parking_blobs):
    if blob.density() >= density_thr and blob.h() > min_cube_height and not is_blob_in_blob(blob, line_blob):
        for parking_wall_blob in parking_blobs:
            if is_blob_in_blob(blob, parking_wall_blob):
                return False
        return True
    return False
```

In addition, we created the following functions in order to avoid code repetition or to break down complicated conditions.

```py
# function that gets the biggest blob by size
def get_biggest_blob(blob_array):
    max_area = 0
    max_blob = None
    for blob in blob_array:
        # we're keeping the biggest parking blob
        if blob.area() > max_area:
            max_area = blob.area()
            max_blob = blob
    return max_blob
```

<br>

# Robot Construction Guide 

## Step 0: Print the 3D parts 

The part files can be found in the `3d-models` folder. We used and recommend the [BambuLab X1-Carbon](https://bambulab.com/en/x1) 3D printer, with the following settings:
 - Material: PLA
 - Layer height: 0.2mm
 - Infill: 20%
 - Supports: Yes
 - Raft: No
 - Brim: Yes

## Step 1: Assemble the steering system 

1. Mount the `servo` on the `chassis` using 2 zip ties, make sure to cut the excess of the zip ties so it doesnt interfere with the steering arm.

2. Attach the `steering axle` to the `servo` using a ⌀ 2mm metal rod, approximately 4-5mm in length.

3. Attach the `servo mount` to the `chassis` using the peg joints.

4. Hold the `steering hubs` between the `chassis` and the `servo mount` and attach them with a ⌀ 2mm metal rod, approximately 20mm in length.

5. Attach the `steering axle` to the `steering hubs` using two ⌀ 2mm metal rod, approximately 20mm in length.

6. Inside the `steering hubs`, place a `Pin Connector Block`(<a href="https://www.bricklink.com/v2/catalog/catalogitem.page?P=39793&idColor=11#T=C&C=11">39793</a>) using pins. Put a `Axle 3L with Stop`(<a href="https://www.bricklink.com/v2/catalog/catalogitem.page?P=24316&idColor=11#T=C&C=11">24316</a>) inside the `Pin Connector Block`.

## Step 2: Assemble the powertrain 
1. Attach the `motor support` to the `chassis` using the peg joints.

2. Attach the `motor` to the `motor support` using the `motor mounts` and *M3* screws.

3. On the `motor`, attach the `gearmotor to axle` and, on the other end, attach a lego `Axle 3L`.

4. On the other end of the `Axle 3L`, attach a lego `Gear 20 Tooth Double Bevel`(<a href="https://www.bricklink.com/v2/catalog/catalogitem.page?P=32269#T=C">32269</a>)

5. The `chasiss` has a place for a differential, attach a `Gear Differential 28 Tooth Bevel`(<a href="https://www.bricklink.com/v2/catalog/catalogitem.page?P=62821b&name=Technic,%20Gear%20Differential%2028%20Tooth%20Bevel%20-%20Inner%20Tabs%20with%20Closed%20Center&category=%5BTechnic,%20Gear%5D#T=C">62821b</a>) there, connected to the `Gear 20 Tooth Double Bevel`. The differential should have 3 `Gear 12 Tooth Bevel`(<a href="https://www.bricklink.com/v2/catalog/catalogitem.page?P=6589#T=C">6589</a>) inside it. The differential should be attached to the `chassis` using lego `Axles 7L`. Where the `Axles 7L` go, there should be a half stud gap in the `chassis`, place a `Bush 1/2`(<a href="https://www.bricklink.com/v2/catalog/catalogitem.page?P=4265c&idColor=3#T=C&C=3">4265c</a>) on each side. This will hold the wheels in place better.

## Step 3: Attach the electronics  

1. Make the `pcb` using a `10x24 prototype board`. Using the `electrical diagram` and the pcb images, solder the connections, and headers and the `voltage regulator`. Place the `Arduino Nano ESP32` and `motor driver` on the pcb. The pcb should be attached to the `pcb plaque` using screws.

2. Place the `battery` in under the `pcb` in the place provided in the `chassis`.

3. Use a `6x12 prototype board` to make a holder for the `power switch` and `start button`, which need to be souldered. On the bottom of the board, soulder headers so that you can use father-father wires to connect to the arduino. We used a longer prototype board and cut it to the desired size. The holder should be attached to the `chassis` using double sided tape. You can also soulder a `led` to the board and connect it to the arduino for debuging purposes.

4. Attach the `IMU` to the `motor support` using screws. Soulder a wire on the `IMU` on the `INT1` pin.

5. Attach the `camera` to the `chassis` using screws. The `camera` should be slighly tilted up.

6. Connect all the wires according to the `electrical diagram`. The `camera` should be connected to the `Arduino` using the `UART` protocol. The `IMU` should be connected to the `Arduino` using the `I2C` protocol. The wires can be store bought, or you can make them yourself. We custom-made our wires to achieve the exact lengths needed and combined certain connections into single Dupont connectors—for example, the camera power, camera UART, and IMU I2C wires are each grouped within individual Dupont connectors.

7. (Optional) All the wires that are longer than needed can be wrapped arrond the `chassis` to make the robot look cleaner. You can use zip ties to secure the wires in place.

## Step 4: Attach the wheels 

1. Attach the front `wheels`(<a href="https://www.bricklink.com/v2/catalog/catalogitem.page?P=39367pb01&idColor=11#T=C&C=11">39367pb01</a>) to the `Axles 3L with Stop`. Use a `Bush 1/2` on each side of the `wheels` to hold them in place.

2. Attach the back `wheels`(<a href="https://www.bricklink.com/v2/catalog/catalogitem.page?P=39367pb01&idColor=11#T=C&C=11">39367pb01</a>)  to the `Axles 7L`. Use a `Bush 1/2` on each side of the `wheels` to hold them in place. Also add spacers so the wheels are on the same level as the front ones.

## Step 5: Final touches 

1. Place a *100g* weight on the back of the robot and one on the `servo mount` to enhance stability and increase grip. The weights should stay in place, but you can stabilize them with some duct tape.

## Step 6: Upload the code 

1. Connect the `Arduino` to your computer using a USB cable.

2. Open the `Arduino IDE` and install the ESP32 board manager.

3. Upload the code to the `Arduino`.

4. Connect the `OpenMV Cam H7` to the your computer using a USB cable.

5. Open the `OpenMV IDE` and upload the code to the `OpenMV Cam H7`.

<br>

# Cost Report 

## Components 

| Component | Quantity | Cost per Unit (€) | Total (€) |
|---|---|---|---|
| 50:1 Micro Metal Gearmotor HPCB 12V | 1 | 21.00 | 21.00 |
| SparkFun Motor Driver - Dual TB6612FNG | 1 | 13.00 | 13.00 |
| Motor Servo MG90S | 1 | 4.00 | 4.00 |
| LiPo Battery (450mAh, 7.4V, 30C) | 1 | 9.00 | 9.00 |
| Arduino Nano ESP32 | 1 | 24.00 | 24.00 |
| Grove - 6-Axis Accelerometer & Gyroscope | 1 | 26.50 | 26.50 |
| OpenMV Cam H7 R2 | 1 | 60.50 | 60.50 |
| Prototype Boards | 2 | 5.00 | 10.00 |
| Metal Rods (2mm diameter, various lengths)  | 6 | 0.50 | 3.00 |
| 100g Fishing Weights | 2 | 5.00 | 10.00 |
| **LEGO Pieces:** | | | |
| Pin Connector Block (39793) | 2 | 0.40 | 0.80 |
| Axle 3L with Stop (24316) | 2 | 0.50 | 1.00 |
| Gear 20 Tooth Double Bevel (32269) | 1 | 1.20 | 1.20 |
| Gear Differential 28 Tooth Bevel (62821b) | 1 | 3.50 | 3.50 |
| Gear 12 Tooth Bevel (6589) | 3 | 0.50 | 1.50 |
| Axles 7L | 2 | 0.60 | 1.20 |
| Bush 1/2 (4265c) | 4 | 0.20 | 0.80 |
| Wheels (39367pb01) | 4 | 2.00 | 8.00 |

**Total for Components:** **€201.00**

---

## 3D Printing Costs 

- **Filament Used:**
  - Prototypes: 1kg of PLA filament
  - Final Parts: 80g of PLA-CF filament
- **PLA-CF Filament Cost:** €32.00 per 1kg
- **PLA Filament Cost:** €25.00 per 1kg

| Filament Use | Weight (g) | Cost (€) |
|---|---|---|
| Prototypes | 1,000 | 25.00 |
| Final Parts | 80 | 2.56 |

**Total for 3D Printing:** **€27.56**

---

## Other Parts Tested 

- **Approximate Cost for Additional Parts Tested:** €150.00

---

## Tools and Equipment 

| Tool | Cost (€) |
|---|---|
| Bambu Lab X1 Carbon 3D Printer | 1,100.00 |
| Soldering Kit | 46.00 |
| Multimeter | 28.00 |
| Miscellaneous Tools (e.g., pliers) | 19.00 |

**Total for Tools and Equipment:** **€1,193.00**

---

## Summary of Costs 

| Category | Total (€) |
|---|---|
| Components | 201.00 |
| 3D Printing | 27.56 |
| Other Parts Tested | 150.00 |
| Tools and Equipment | 1,193.00  |
| Shipping Approximation | 80.00 |

**Grand Total:** **€1,651.56**

---

*Note: Costs are approximate and based on current exchange rates and market prices.*

<br>

# Randomizer 

To ensure the robot's ability to adapt to any course, we developed a randomizer that generates a random sequence of colors and positions for the cubes. You can find this web application at the following link: https://nerdvana.ro/wro-fe/

<br>

# Resources 

## Images 
<li> DC Motor - https://a.pololu-files.com/picture/0J10610.1200.jpg?204e9b873c23906503616db5c4950010
<li> MG90S Servo motor - https://www.robotistan.com/tower-pro-mg90s-micro-servo-motor-continuously-rotating-37080-99-B.jpg
<li> Sparkfun Motor Driver - https://cdn.sparkfun.com//assets/parts/1/2/4/8/2/14450a-01.jpg
<li> Arduino Nano ESP32 - https://ardushop.ro/7735-thickbox_default/arduino-nano-esp32-with-headers.jpg
<li> OpenMV Cam H7 R2 - https://openmv.io/cdn/shop/products/new-cam-v4-angle-web_3a8c4a96-13b4-4d3f-95f8-c3b8a8cc8e05_1000x_crop_center.jpg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
<li> LiPo Battery - https://hpi-racing.ro/29739-medium_default/acumulator-lipo-gens-ace-g-tech-soaring-450mah-74v-30c-2s1p-cu-jst-syp.jpg
<li> Grove BMI088 Gyroscope - https://files.seeedstudio.com/wiki/Grove-6-Axis_Accelerometer-Gyroscope-BMI088/img/main.jpg
<li> Linear voltage regulator - https://m.media-amazon.com/images/I/71gro1yTESL._SL1500_.jpg

<br>

## Copyright 

```
MIT License

Permission is hereby granted, free of charge, to any person obtaining a copy of this software and associated documentation files (the "Software"), to deal in the Software without restriction, including without limitation the rights to use, copy, modify, merge, publish, distribute, sublicense, and/or sell copies of the Software, and to permit persons to whom the Software is furnished to do so, subject to the following conditions:

The above copyright notice and this permission notice shall be included in all copies or substantial portions of the Software.

THE SOFTWARE IS PROVIDED "AS IS", WITHOUT WARRANTY OF ANY KIND, EXPRESS OR IMPLIED, INCLUDING BUT NOT LIMITED TO THE WARRANTIES OF MERCHANTABILITY, FITNESS FOR A PARTICULAR PURPOSE AND NONINFRINGEMENT. IN NO EVENT SHALL THE AUTHORS OR COPYRIGHT HOLDERS BE LIABLE FOR ANY CLAIM, DAMAGES OR OTHER LIABILITY, WHETHER IN AN ACTION OF CONTRACT, TORT OR OTHERWISE, ARISING FROM, OUT OF OR IN CONNECTION WITH THE SOFTWARE OR THE USE OR OTHER DEALINGS IN THE SOFTWARE.

© 2024 Nerdvana Romania
```

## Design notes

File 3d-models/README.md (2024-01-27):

# 3D Models

This directory contains 3D models of the robot. The models are in the [STL](https://en.wikipedia.org/wiki/STL_(file_format)) format.

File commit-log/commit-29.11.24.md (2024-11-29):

# Commit - 29/11/2024

## Calibrated the code

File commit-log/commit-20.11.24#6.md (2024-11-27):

# Commit - 20/11/2024#6

## Added new electrical diagram and new code

Improved the robustness of the code and modified the electrical diagram since we don't power up the camera through the battery input anymore, but by using the VIN and GND pins since it's more stable this way. The reason is that we didn't find the perfect port, so we made one ourselves, but with time it got less and less stable. Therefore, using the VIN and GND pins provides the best grip ever.

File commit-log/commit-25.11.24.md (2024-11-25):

# Commit - 25/11/2024

## Added right code verification

Added a small piece of code that flashes the leds differently if we're running the quali code or the final code so that we know that we're running the right program.

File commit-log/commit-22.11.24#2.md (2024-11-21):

# Commit - 22/11/2024#2

## Updated documentation with additional camera code

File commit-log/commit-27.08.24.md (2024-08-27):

# Commit - 27/08/2024

## Modified the strategy

We modified our approach: instead of focusing on a wall centered solution in which our turns depended on the wall size as seen by the camera, we take turns based on the corner lines. In addition, we made our cube avoidance algorithm more agile and more robust, now having a single code that can solve both rounds.

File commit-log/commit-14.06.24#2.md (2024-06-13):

# Commit - 14/06/2024 #2

## Added 3d printed parts' dimensions drawings and updated the README

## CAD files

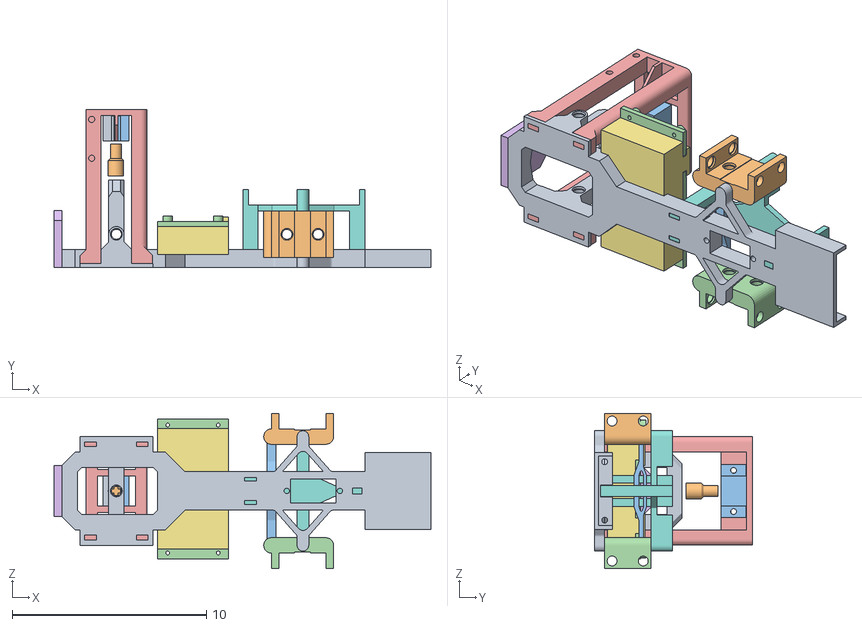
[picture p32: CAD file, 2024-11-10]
3d-models/robot_v136.obj
19.4 x 8.11 x 8.00
Wheel_Hub_Right
Steer_Axle
Wheel_Hub_Left

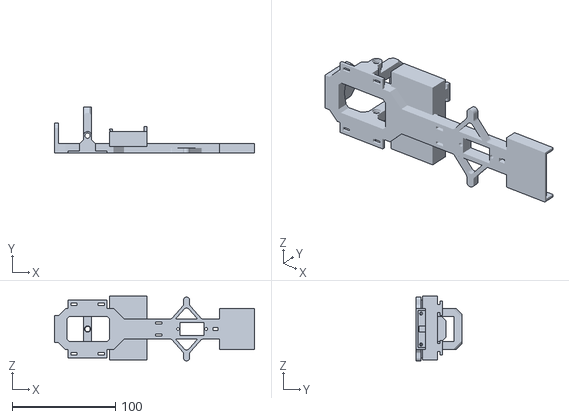
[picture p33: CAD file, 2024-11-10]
3d-models/chassis_v7.stl
194.0 x 45.0 x 63.0

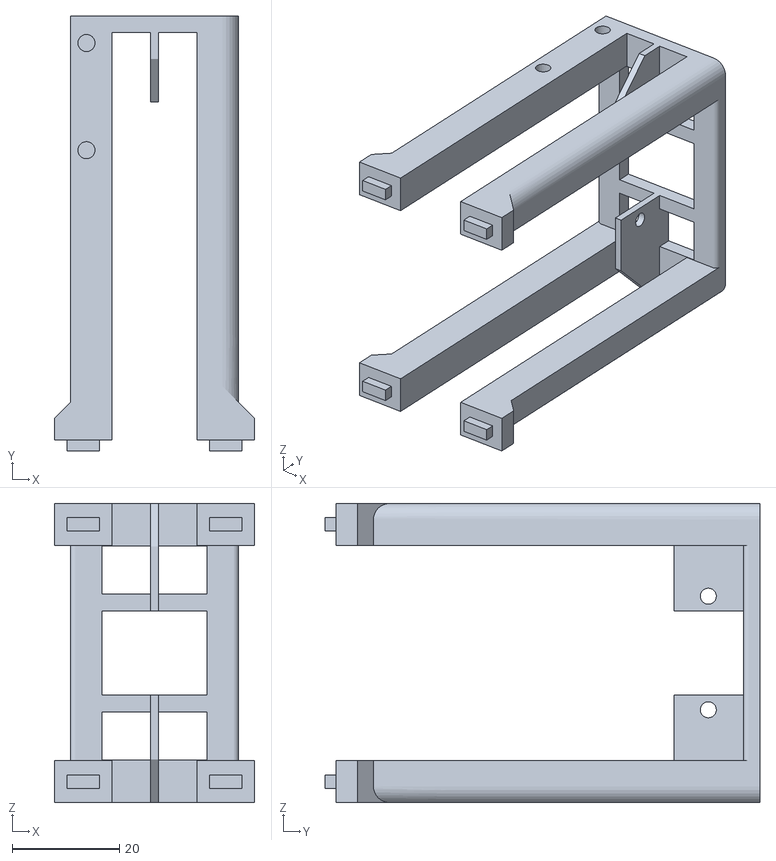
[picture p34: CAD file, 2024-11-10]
3d-models/motor_support_v9.stl
37.4 x 81.1 x 55.8

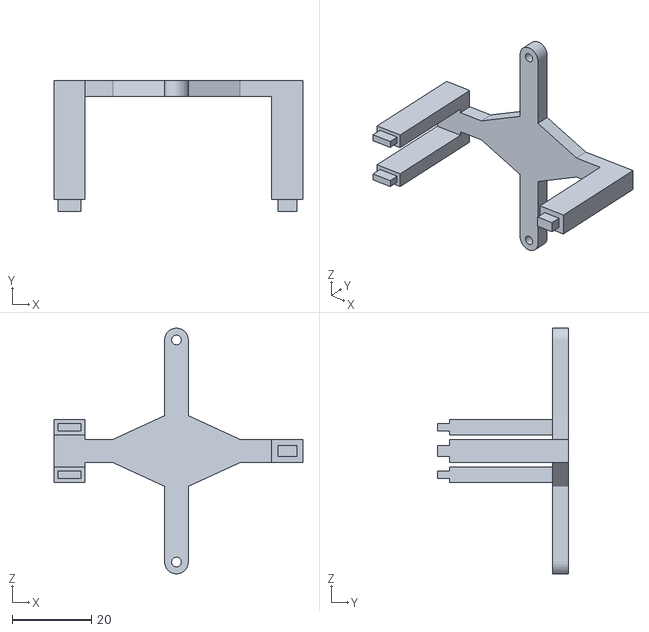
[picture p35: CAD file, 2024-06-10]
3d-models/servo_mount_v8.stl
62.8 x 33.0 x 62.0

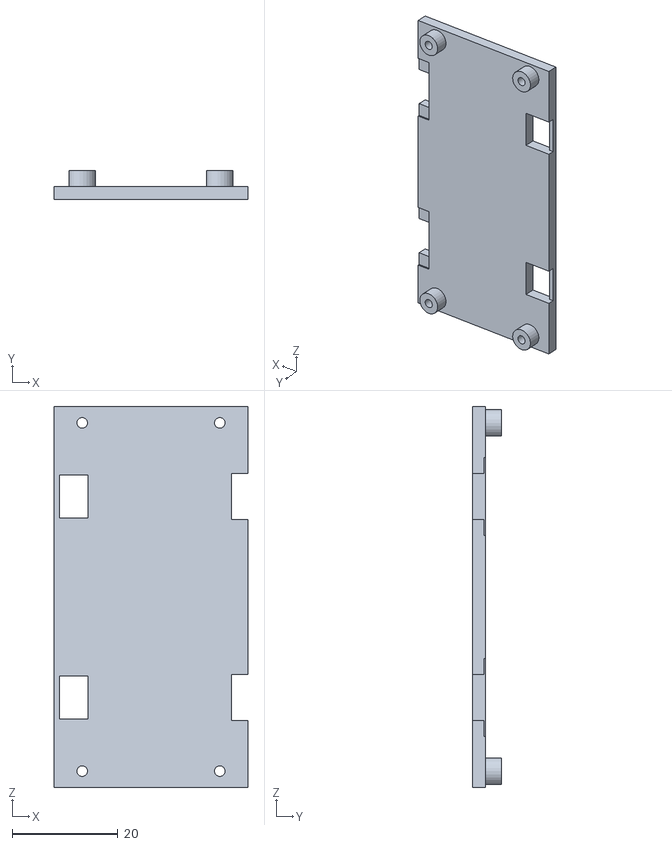
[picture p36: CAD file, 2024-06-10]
3d-models/pcb_plaque_v5.stl
36.6 x 5.50 x 72.0

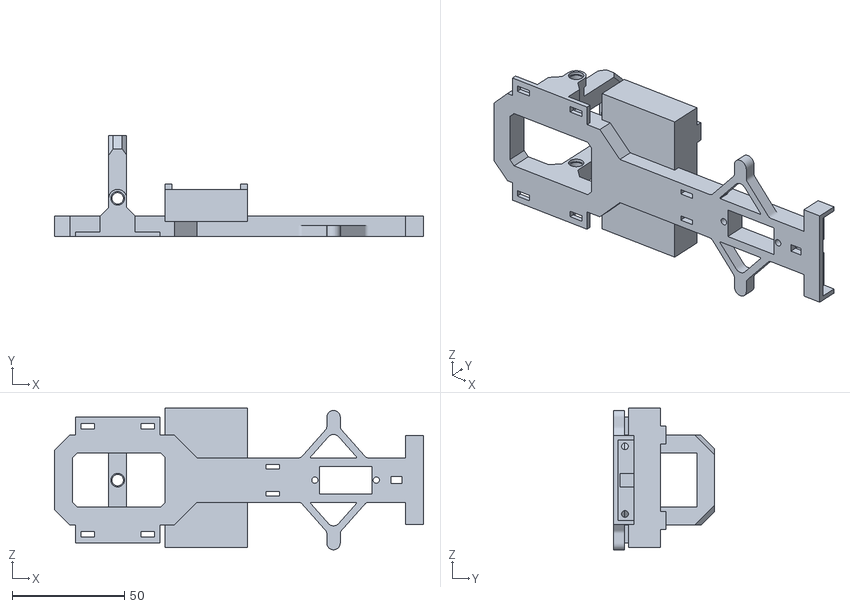
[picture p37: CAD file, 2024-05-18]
3d-models/chasis_v4.stl
164.1 x 45.0 x 63.0

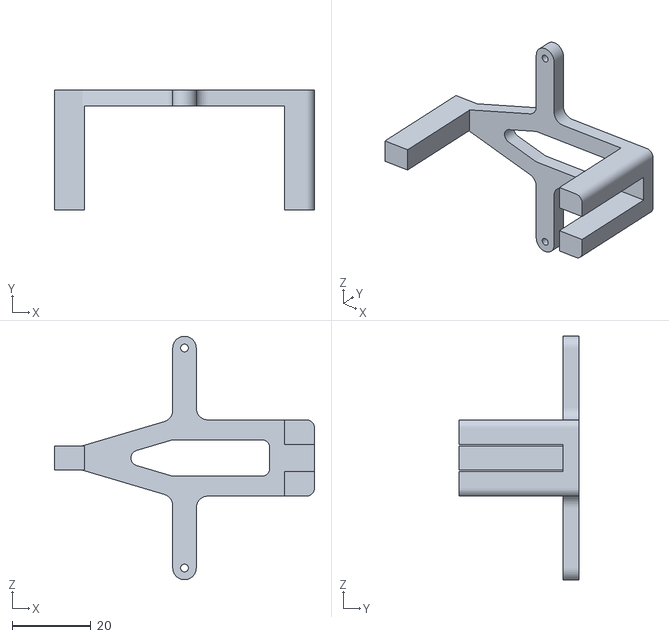
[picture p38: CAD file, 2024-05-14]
3d-models/steering_mount_v4.stl
66.2 x 30.5 x 62.0

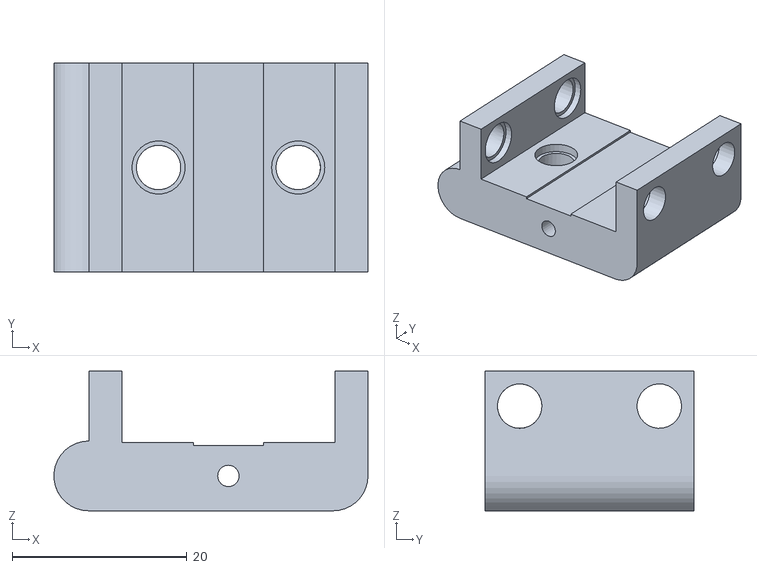
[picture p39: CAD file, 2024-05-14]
3d-models/steering_hub_right_v5.stl
36.0 x 24.0 x 16.0

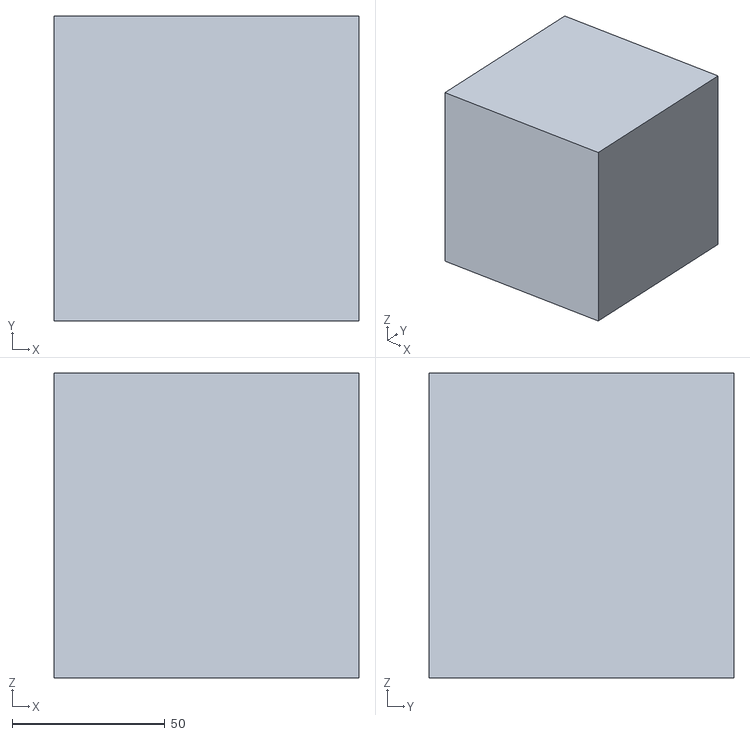
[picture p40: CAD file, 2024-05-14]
3d-models/cube.stl
100.0 x 100.0 x 100.0

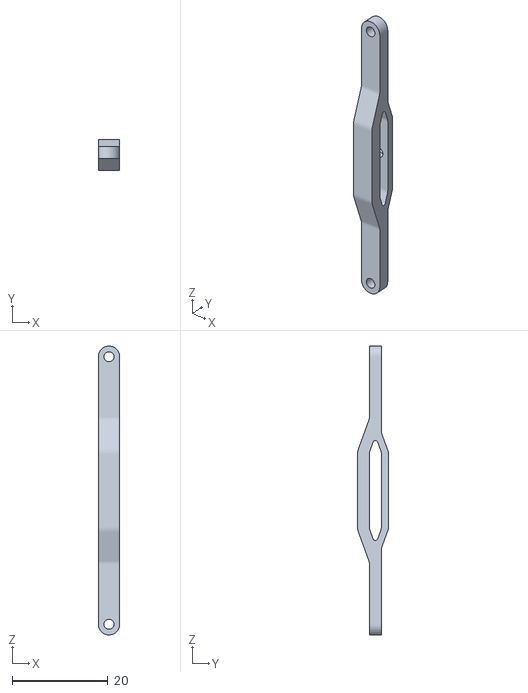
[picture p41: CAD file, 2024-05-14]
3d-models/servo_axle_v7.stl
4.50 x 6.50 x 60.5

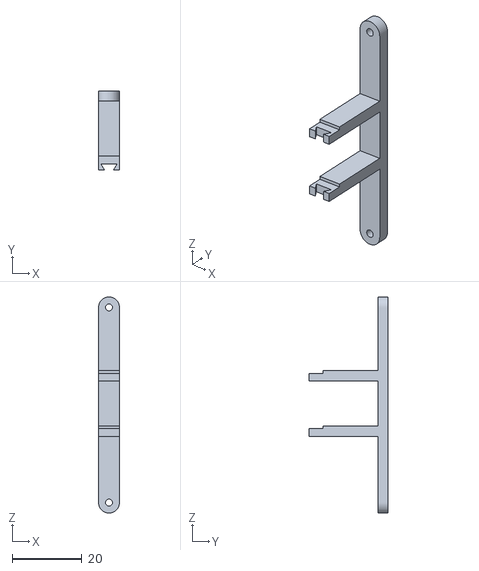
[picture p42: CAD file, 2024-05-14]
3d-models/steering_mount_top_part.stl
6.00 x 22.8 x 62.0

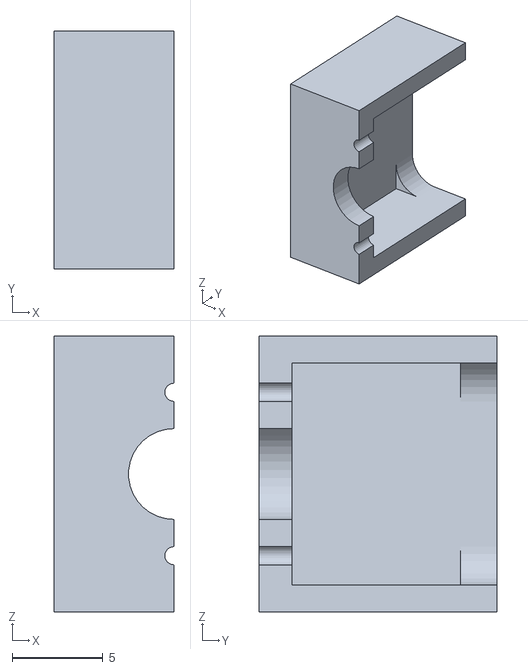
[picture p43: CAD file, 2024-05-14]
3d-models/micromotor_half_v1.stl
6.60 x 13.1 x 15.2

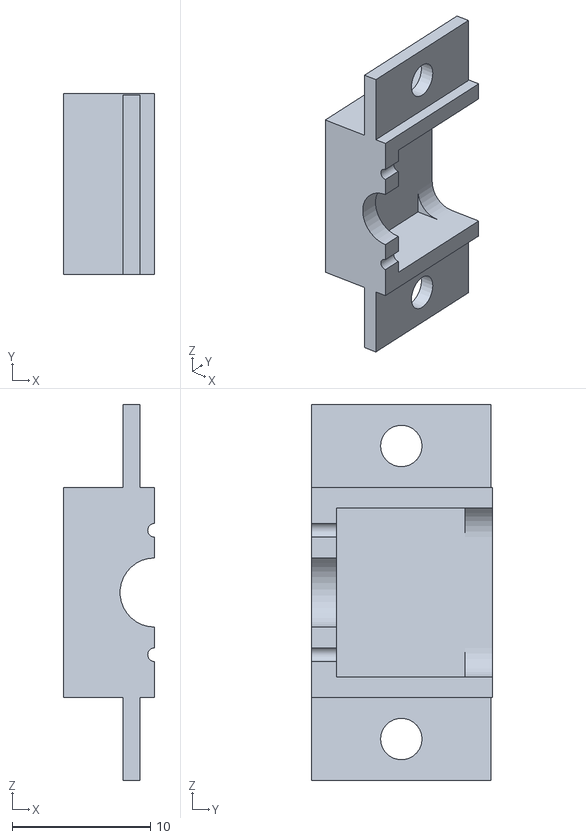
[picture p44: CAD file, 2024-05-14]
3d-models/motor_mount_v3.stl
6.60 x 13.1 x 27.2

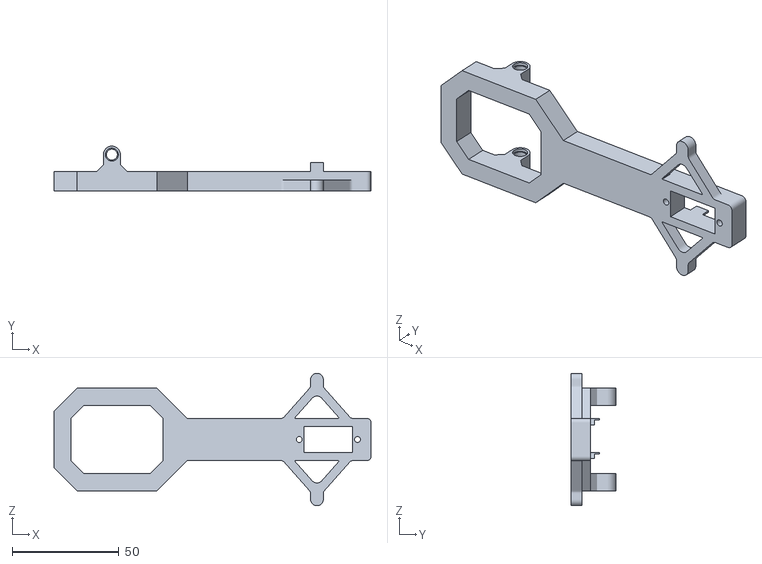
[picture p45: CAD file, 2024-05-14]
3d-models/robot_v1 v38.stl
148.4 x 21.0 x 62.0

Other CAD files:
3d-models/steering_axle_v8.stl
3d-models/steering_hub_left_v5.stl
3d-models/robot_v1 v13.stl
3d-models/motor_to_axle_v2.stl
3d-models/chasis_v1.stl
3d-models/chasis_v2.stl
3d-models/chasis_v3.stl
3d-models/motor_mount_v2.stl
3d-models/motor_support_v1.stl
3d-models/motor_support_v2.stl
3d-models/motor_support_v3.stl
3d-models/motor_support_v4.stl
3d-models/motor_support_v5.stl
3d-models/motor_support_v6.stl
3d-models/motor_to_axle_v1.stl
3d-models/pcb_plaque_v1.stl
3d-models/pcb_plaque_v2.stl
3d-models/screw_test.stl
3d-models/screw_test_ v2.stl
3d-models/screw_test_v3.stl
3d-models/servo_mount_v1.stl
3d-models/servo_mount_v2.stl
3d-models/servo_mount_v4.stl
3d-models/servo_mount_v5.stl
3d-models/servo_mount_v6.stl
3d-models/servo_mount_v7.stl
3d-models/steering_axle_v1.stl
3d-models/steering_axle_v2.stl
3d-models/steering_axle_v3.stl
3d-models/steering_axle_v4.stl
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

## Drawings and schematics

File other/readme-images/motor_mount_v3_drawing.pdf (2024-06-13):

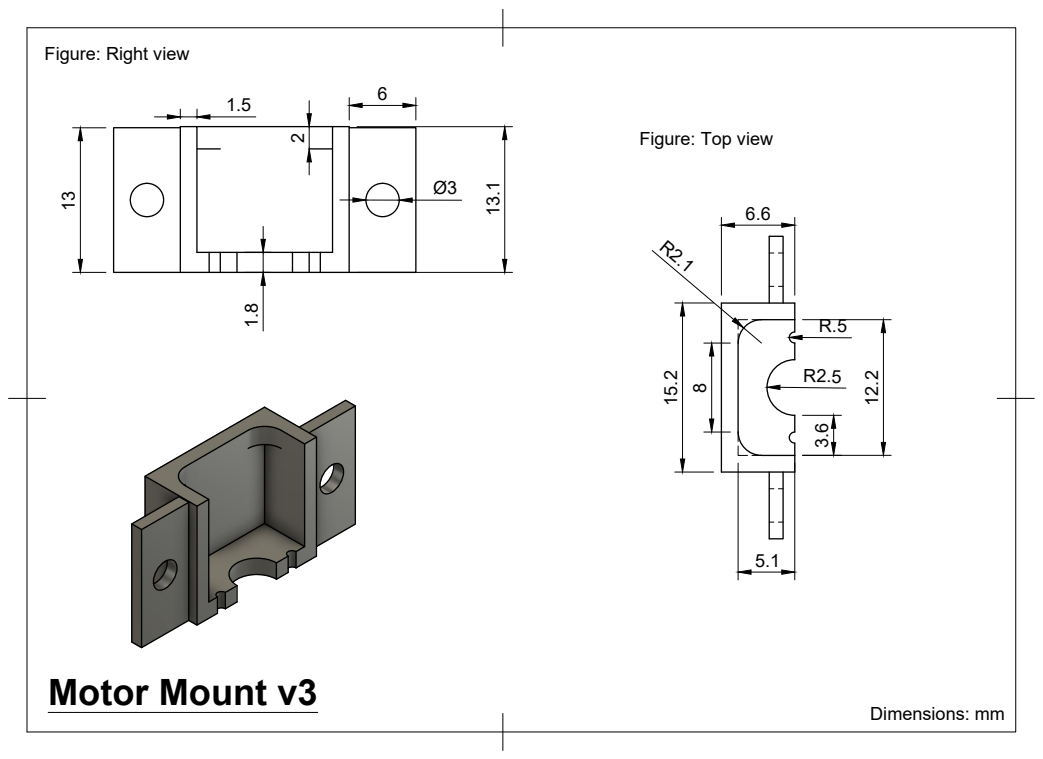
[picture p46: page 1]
Motor Mount v3; Dimensions: mm 15.2

Figure: Right view

Figure: Top view

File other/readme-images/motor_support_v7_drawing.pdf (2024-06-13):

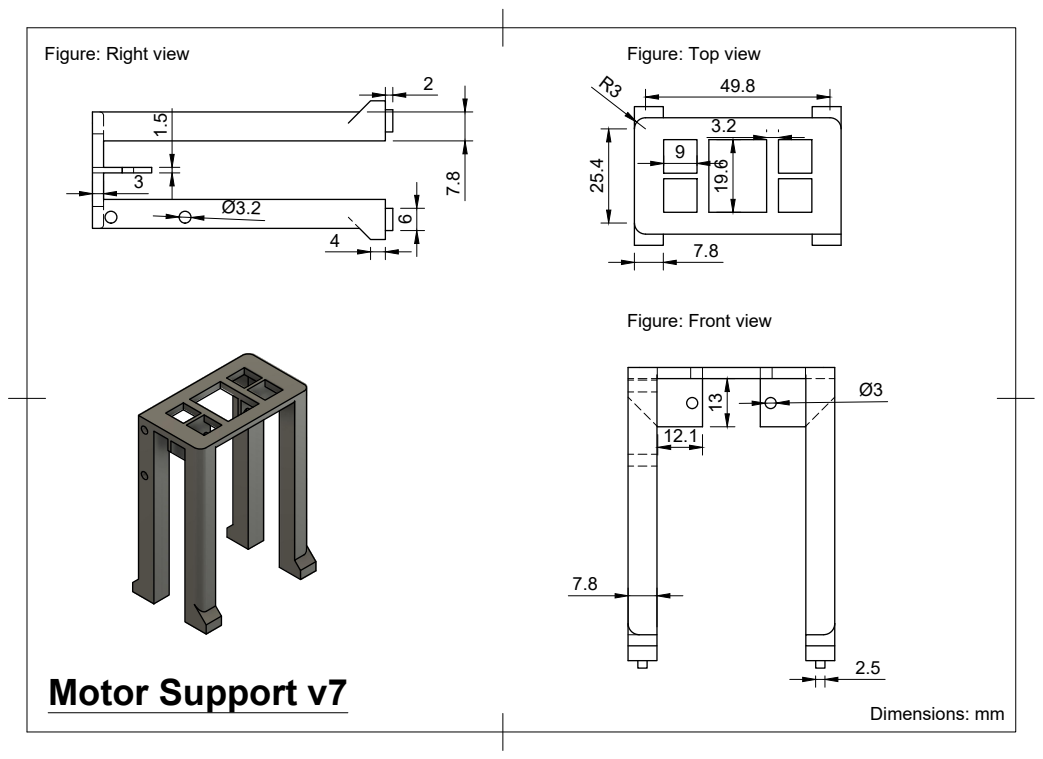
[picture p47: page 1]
Motor Support v7; Figure: Right view; Figure: Top view; Dimensions: mm

Figure: Front view 1.5

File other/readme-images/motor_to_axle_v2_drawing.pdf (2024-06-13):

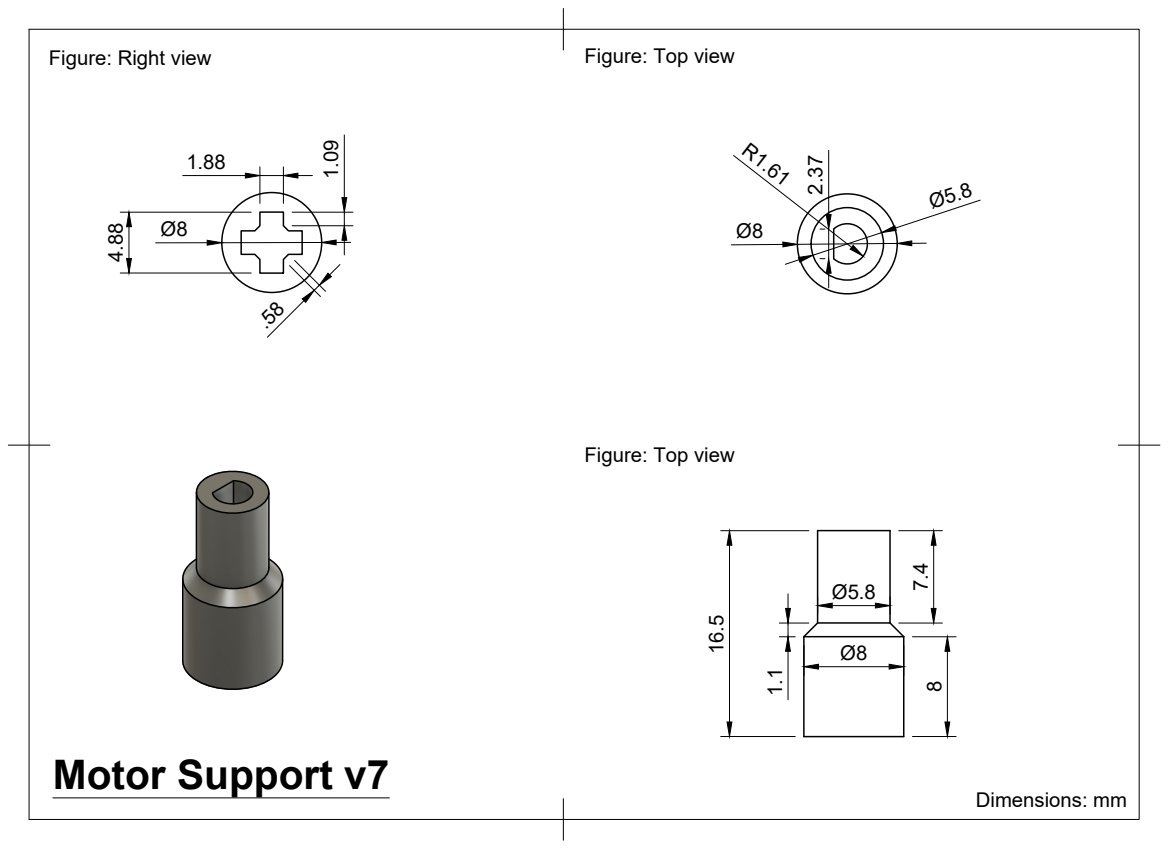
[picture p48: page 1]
Motor Support v7; Figure: Right view; Figure: Top view; Dimensions: mm

Figure: Top view

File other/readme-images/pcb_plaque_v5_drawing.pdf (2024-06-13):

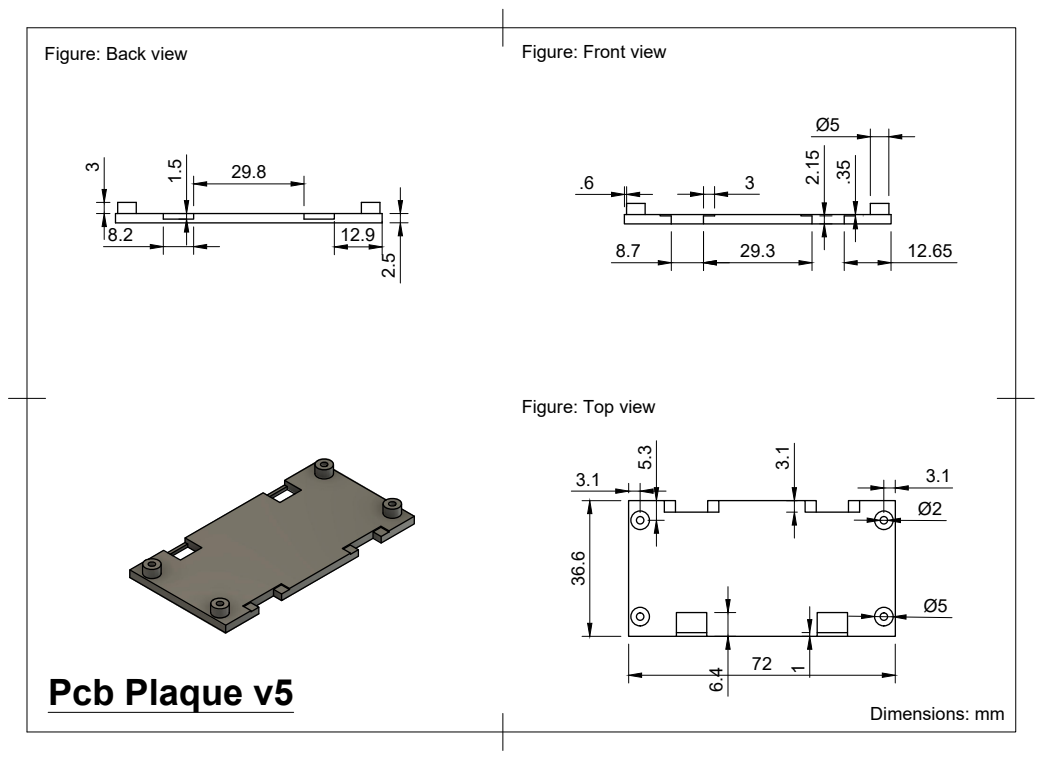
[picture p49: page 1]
Pcb Plaque v5; Figure: Back view; Figure: Front view; Dimensions: mm

Figure: Top view

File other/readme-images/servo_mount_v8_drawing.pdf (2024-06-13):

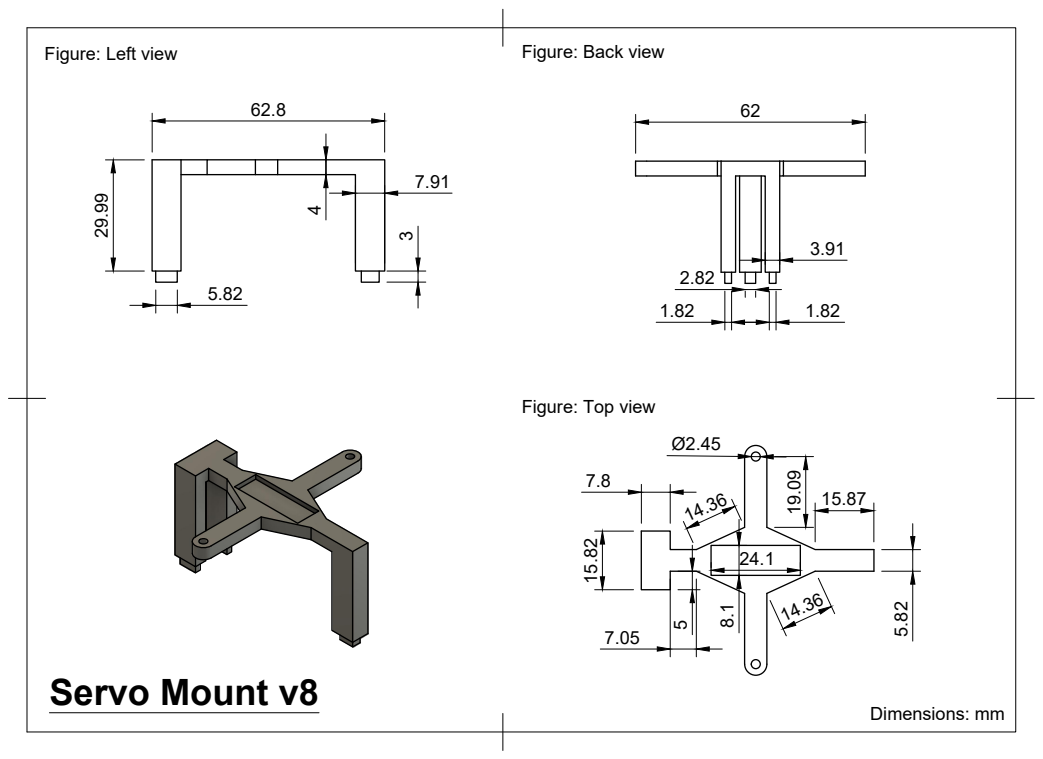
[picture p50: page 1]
Servo Mount v8; Figure: Left view; Figure: Back view; Dimensions: mm

Figure: Top view 15.82

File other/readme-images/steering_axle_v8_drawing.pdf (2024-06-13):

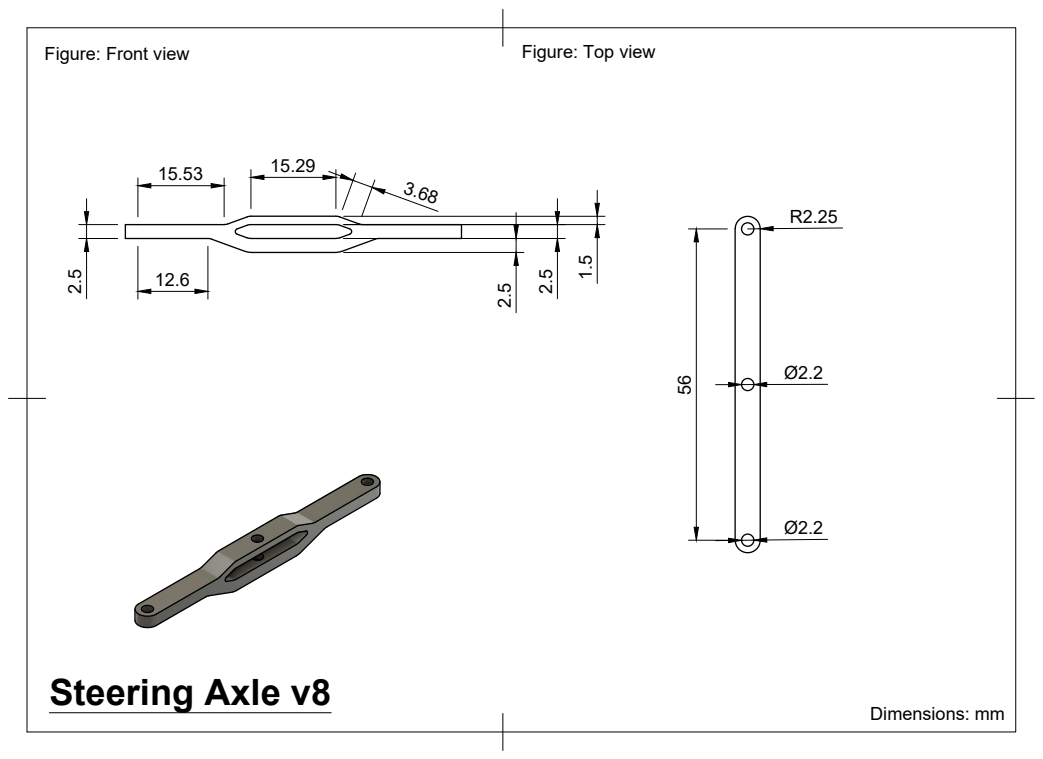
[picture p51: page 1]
Steering Axle v8; Figure: Front view; Figure: Top view; Dimensions: mm

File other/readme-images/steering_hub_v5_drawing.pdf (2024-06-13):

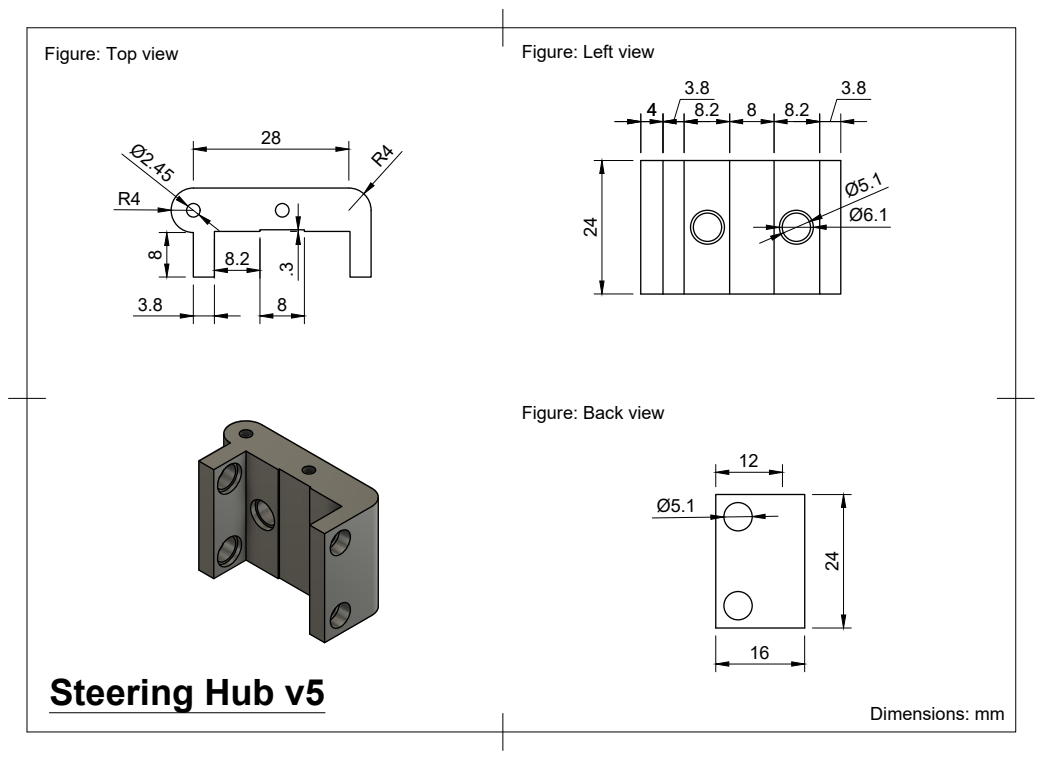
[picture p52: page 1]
Steering Hub v5; Figure: Top view; Figure: Left view; Dimensions: mm

Figure: Back view

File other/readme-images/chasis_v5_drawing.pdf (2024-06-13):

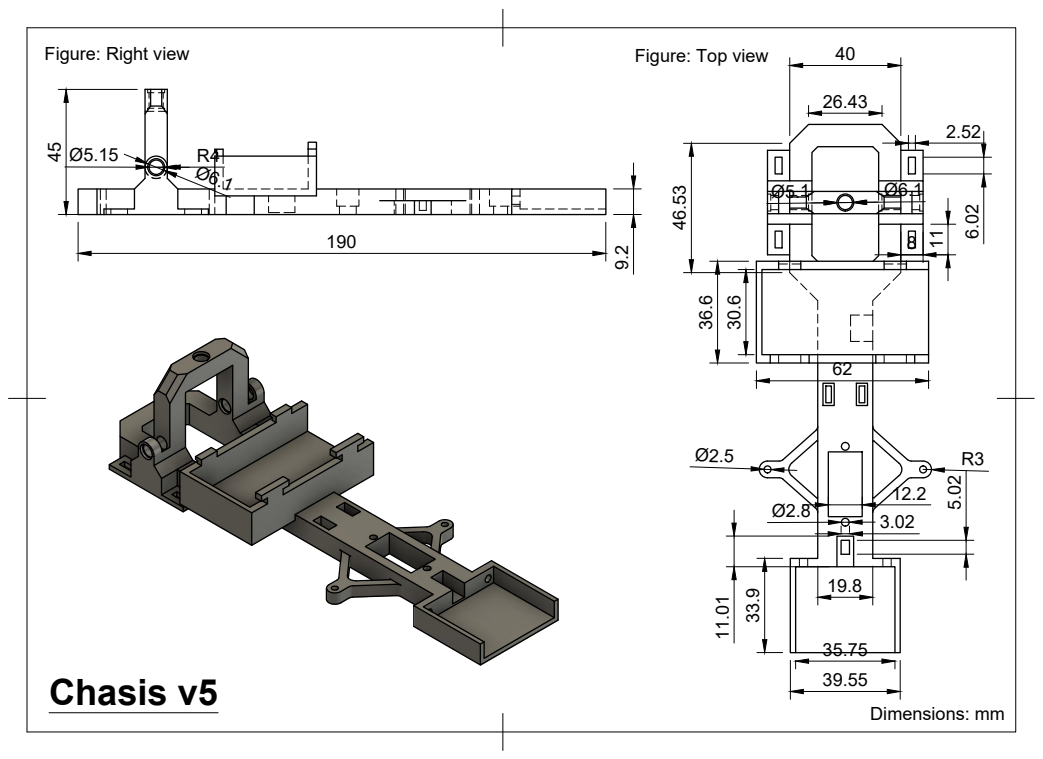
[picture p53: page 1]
Chasis v5; Figure: Right view; Figure: Top view; Dimensions: mm

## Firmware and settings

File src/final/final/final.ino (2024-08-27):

#include <math.h>
#include <Encoder.h>
#include <ESP32Servo.h>
#include <Wire.h>
#include "BMI088.h"

// -----Button and Debug led-----
#define BTN_PIN A3
#define DEBUG_LED D12

void setup() {
  setup_function();
}

bool is_running = false;

uint32_t last_rotate = 0, time_elapsed = 0;
int turns = 0, freq = 0;

void loop() {
  int is_start_btn_on = digitalRead(BTN_PIN);
  read_gyro(false);
  if (!is_running && is_start_btn_on == LOW) {
    is_running = true;
    
    digitalWrite(LED_BUILTIN, LOW);
    digitalWrite(DEBUG_LED, LOW);
    
    last_rotate = millis();
    // time_elapsed = millis();
    // freq = 0;
  }
  if (is_running) {
    loop_function();
  }
}

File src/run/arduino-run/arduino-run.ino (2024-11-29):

#include <math.h>
#include <Encoder.h>
#include <ESP32Servo.h>
#include <Wire.h>
#include "BMI088.h"

#define FINAL true

// -----Button and Debug led-----
#define BTN_PIN A3
#define DEBUG_LED D12

void setup() {
  setup_function();
}

bool is_running = false;

uint32_t last_rotate = 0, time_elapsed = 0;

void loop() {
  int is_start_btn_on = digitalRead(BTN_PIN); // wait for the button to be pressed
  read_gyro(false); // flush the data
  flush_messages();
  if (!is_running && is_start_btn_on == LOW) { // if we press the button and the program isn't running
    is_running = true; // start the program
    
    digitalWrite(LED_BUILTIN, LOW);
    digitalWrite(DEBUG_LED, LOW); // turn off the debugging leds

    // custom_delay(3000);
    
    last_rotate = millis(); // initialize times
    // time_elapsed = millis();
    // freq = 0;
  }
  if (is_running) { // if the program is running, execute one iteration of the loop function
    loop_function();
  }
}

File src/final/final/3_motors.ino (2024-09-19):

// -----Servo-----
#define SERVO_PIN D2
#define ANGLE_MIN 8 // 10
#define ANGLE_MID 48 // 50
#define ANGLE_MAX 88 // 90
#define ANGLE_VARIANCE_THRESHOLD (ANGLE_MAX * 0.4)
#define STEP 4
Servo servo;
double goal_deg;

// -----Motor_Drive-----
#define PWMA A2
#define AIN2 A1
#define AIN1 A0
#define DRIVER_PWM_CHANNEL 1
#define PWM_FREQ 5000 // 5 kHz
#define PWM_RES 10 // 10-bit resolution

// -----Encoder-----
#define ENCODER_PIN1 D5
#define ENCODER_PIN2 D4
#define GEAR_RATIO 1. / 50
#define WHEEL_DIAM 49.5
Encoder myEnc(ENCODER_PIN1, ENCODER_PIN2);

void motor_driver_setup() {
  ledcSetup(DRIVER_PWM_CHANNEL, PWM_FREQ, PWM_RES);
  ledcAttachPin(PWMA, DRIVER_PWM_CHANNEL);

  pinMode(AIN1, OUTPUT);
  pinMode(AIN2, OUTPUT);
}

void servo_setup() {
  servo.attach(SERVO_PIN);
  for (int deg = servo.read() - 1; deg >= ANGLE_MIN; deg--)
    servo.write(deg);
  delay(500);
  // Serial.println("after ANGLE_MIN");
  for (int deg = servo.read() + 1; deg <= ANGLE_MID; deg++)
    servo.write(deg);
  // Serial.println("after ANGLE_MID");
  for (int deg = servo.read() + 1; deg <= ANGLE_MAX; deg++)
    servo.write(deg);
  delay(500);
  // Serial.println("after ANGLE_MAX");
  for (int deg = servo.read() - 1; deg >= ANGLE_MID; deg--)
    servo.write(deg);
  delay(500);
  // Serial.println("after ANGLE_MID");
  goal_deg = ANGLE_MID;
}

void move_motor(double speed) {  // move the motor with a given speed in the [0, 100] interval
  int dir = 1;
  if (speed < 0) {
    dir = -1;
    speed *= -1;
  }
  else if (speed == 0) {
    dir = 0;
  }
  speed = map_double(speed, 0, 100, 0, 1023);
  if (dir == 1) {
    digitalWrite(AIN1, HIGH);
    digitalWrite(AIN2, LOW);
  }
  else if (dir == -1) {
    digitalWrite(AIN1, LOW);
    digitalWrite(AIN2, HIGH);
  }
  else {
    digitalWrite(AIN1, LOW);
    digitalWrite(AIN2, LOW);
  }
  ledcWrite(DRIVER_PWM_CHANNEL, (int)speed);
}

void custom_delay(long long delay_time) {
  long long start_time = millis();
  while (millis() - start_time < delay_time) {
    read_gyro(false);
    while (Serial0.available() > 0) { // if we have some characters waiting
      Serial0.read(); // flush the character
    }
  }
}

void motor_break(long long break_time) {
  move_motor(-3);
  custom_delay(break_time);
}

double read_motor_cm() {  // getting the distance driven by the motor in cm
  return GEAR_RATIO * WHEEL_DIAM * M_PI * (double)myEnc.read() / 12 / 10;
}

void move_servo(double angle) {  // move the servo to the angle checkpoint by setting the goal degrees to the angle value
  goal_deg = map_double(angle, -1, 1, ANGLE_MIN, ANGLE_MAX);
}

void update_servo() {
  int current_angle_servo = servo.read();
  // print_angles();
  if (abs(current_angle_servo - goal_deg) >= ANGLE_VARIANCE_THRESHOLD) {
    servo.write(goal_deg);
  }
  else {
    if (current_angle_servo < goal_deg) {
      servo.write(min(current_angle_servo + STEP, ANGLE_MAX));
    }
    else if (current_angle_servo > goal_deg) {
      servo.write(max(current_angle_servo - STEP, ANGLE_MIN));
    }
  }
}

void move_until_angle(double speed, double gyro_offset) {
  int sign = 1;
  if (speed < 0)
    sign = -1;
  read_gyro(false);
  double err = gyro_offset - gx;
  while (abs(err) >= 10) {
    read_gyro(false);
    err = gyro_offset - gx;
    pid_error_gyro = (err) * kp_gyro + (pid_error_gyro - pid_last_error_gyro) * kd_gyro;
    pid_last_error_gyro = pid_error_gyro;
    move_servo(pid_error_gyro * sign);
    update_servo();
    move_motor(speed);
    while (Serial0.available() > 0) { // if we have some characters waiting
      Serial0.read(); // flush the character
    }
  }
}

void move_cm_gyro(double dis, double speed, double gyro_offset) {
  double start_cm = read_motor_cm();
  int sign = 1;
  if (speed < 0)
    sign = -1;
  while (abs(read_motor_cm() - start_cm) < dis) {
    read_gyro(false);
    double err = gyro_offset - gx;
    pid_error_gyro = (err) * kp_gyro + (pid_error_gyro - pid_last_error_gyro) * kd_gyro;
    pid_last_error_gyro = pid_error_gyro;
    move_servo(pid_error_gyro * sign);
    update_servo();
    move_motor(speed);
    while (Serial0.available() > 0) { // if we have some characters waiting
      Serial0.read(); // flush the character
    }
  }
}

void print_angles() {  // for debugging reasons
  int current_angle = servo.read();
  Serial.print("goal: ");
  Serial.print(goal_deg);
  Serial.print("\tcurrent: ");
  Serial.println(current_angle);
}

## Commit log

2024-03-30 Commit - 30/03/2024 | Added servo functions
2024-05-14 Commit - 14/05/2024 | Added robot 3d models
    [chasis_v1.stl, chasis_v2.stl, chasis_v3.stl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]
2024-05-18 Commit - 18/05/2024 | Added robot 3d models
    [chasis_v4.stl, motor_support_v6.stl]
2024-05-21 Commit - 21/05/2024 | Added electrical diagram and updated Arduino functions
2024-06-10 Commit - 10/06/2024 | Moved 3d models in their respective directories
    [chasis_v1.stl, chasis_v2.stl, chasis_v3.stl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]
2024-06-13 Commit - 14/06/2024 #2 | Added 3d printed parts' dimensions drawings and updated the README
2024-07-18 Commit - 18/07/2024
    [robot_v126.obj]
2024-11-10 Commit - 10/11/24#2 | Added latests robot parts 3d models
    [chasis_v5.stl, chassis_v7.stl, motor_support_v7.stl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]
2024-11-21 Commit - 22/11/2024#2 | Updated documentation with additional camera code
2024-11-29 Commit - 29/11/2024 | Calibrated the code
